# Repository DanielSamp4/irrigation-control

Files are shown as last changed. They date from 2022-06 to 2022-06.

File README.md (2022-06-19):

# Control plants irrigation using ESP32

A challenge made by Neurobots

# Overview

This project consist in creat a system that can irrigate plants based on day period and degree of humidity. This system have to be pownred by a battery of 3.7v 

### System

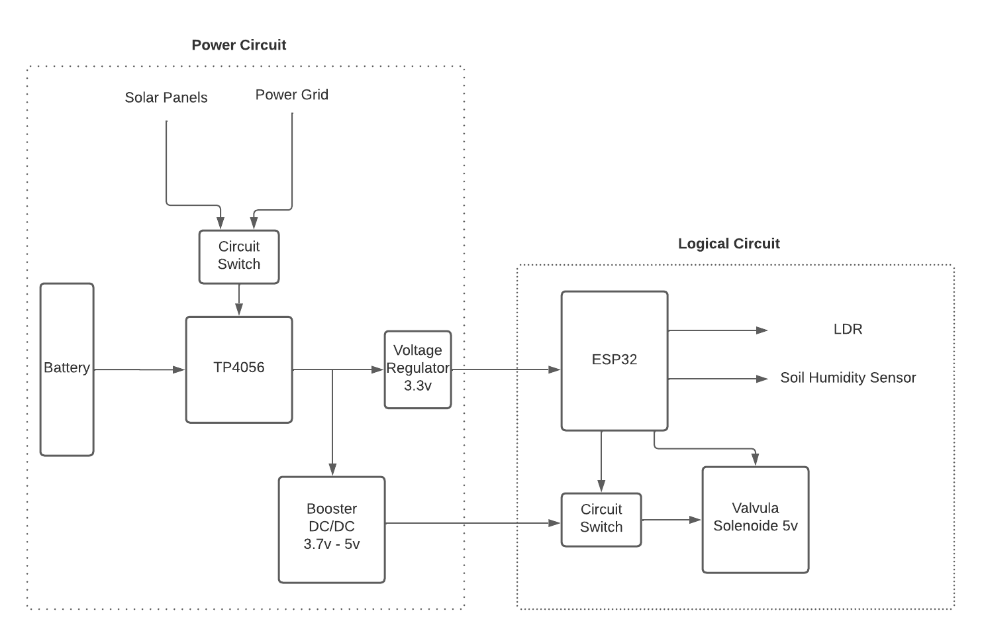
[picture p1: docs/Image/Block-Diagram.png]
Block Diagram
<div align="center">

 In summary, the system is made to charge the battery with solar pannels or power grid (giving priority to the power grid), and power a ESP32 that will be the brain operation, that will check if LDR and Soil Hmidity Sensor get in determinate condition, and will trigger the circuit switch to activate the solenoid, therefore irrigating a plant.

 The Soil Hmidity Sensor, Solenoid and LDR have conectors attached to the PCB (See Hardware Section) to connect them, and the user feel free to use them.
 
### Power Circuit
lithium batteries can be dangerous if not charged properly and that's why the TP4056 is useful as it stops over voltage and current charging by detecting specific voltage conditions. You should never use the TP4056 as a charger and as a load driver at the same time. For this we will use a PMOSFET that will function like a controlled switch that disconnects the battery when external power is applied. The TP4056 still charges the battery but without a load. Power to the load is supplied from the power source directly.

To know more about the right way to use TP4056 see https://www.best-microcontroller-projects.com/tp4056.html

### Logical Circuit

Both LDR and Sensor Humidity are analog devices, therefore can be atached to any ADC GPIO of ESP32, i choose GPIO 34 and 35 (See Firmware Section).

For Activate the solenoid, must be a output GPIO (anyone except 34, 35, 36, 39 because they are input only) and the circuit switch will be a NMOSFET with gate connect to GPIO, drain connect to GND from the solenoid and source connect to GND from the circuit, with this configuration when GPIO is high the NMOSFET will connect the GND from NMOSFET with the GND from de circuit and de valvula solenoid will open. I will connect to GPIO 25 and will use PWM signal to see if will genarate some kind of water flow control from solenoid.

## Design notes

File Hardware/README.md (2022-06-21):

# Hardware

### Schematic
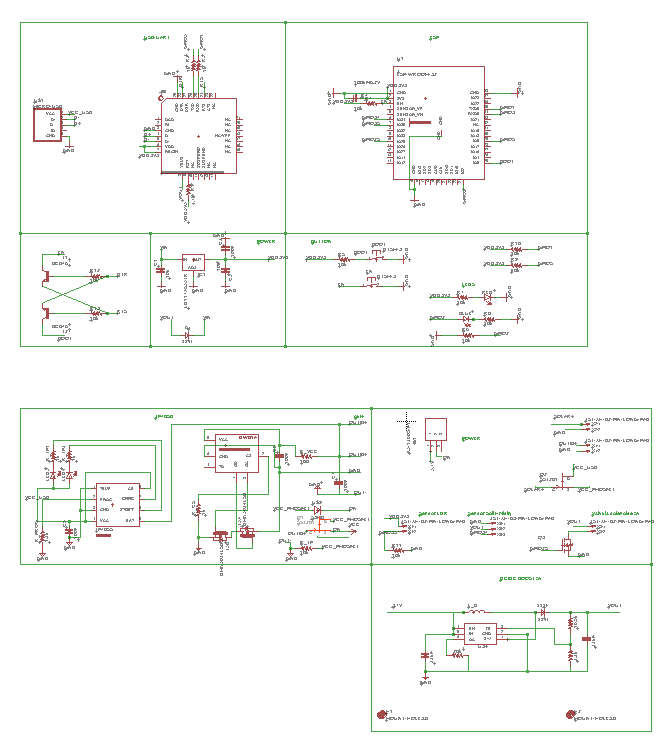
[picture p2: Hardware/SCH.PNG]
Schematic
<div align="center">

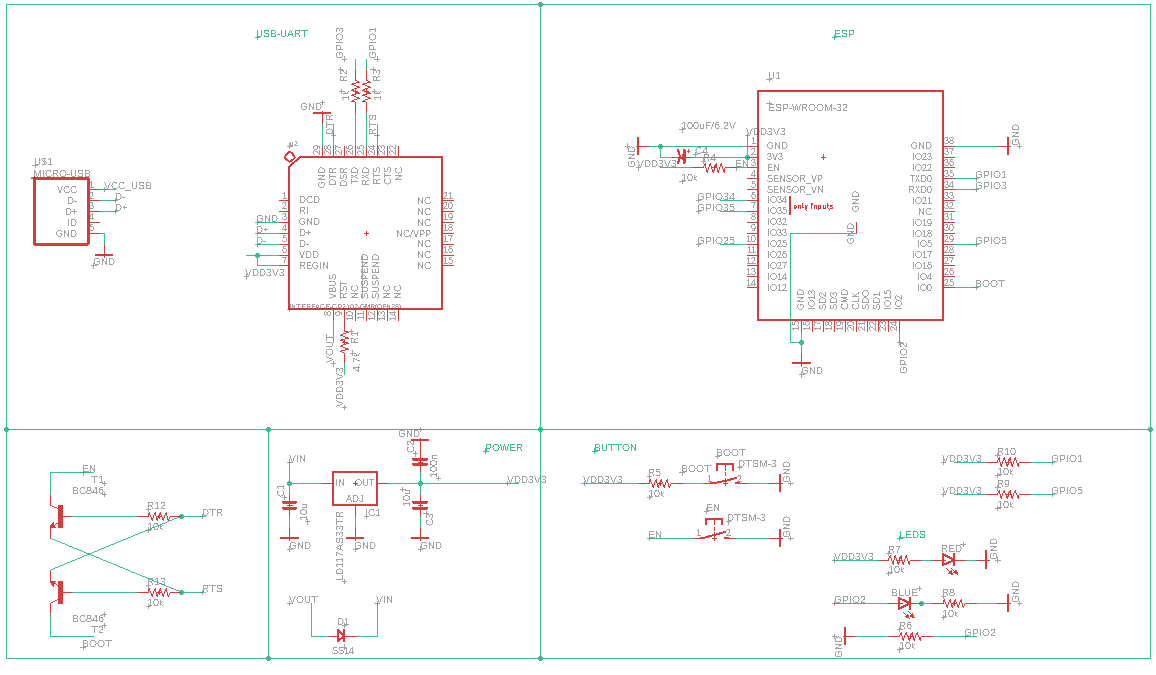
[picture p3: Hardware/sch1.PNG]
Schematic part 1
<div align="center">

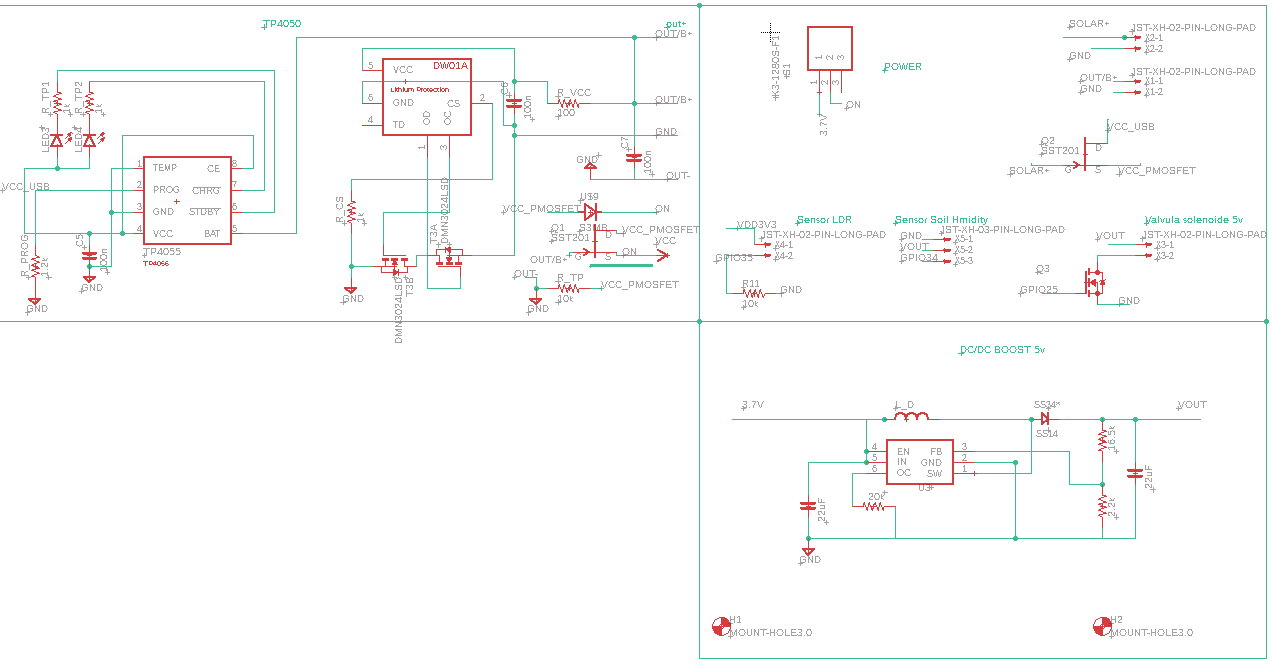
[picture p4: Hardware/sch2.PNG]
Schematic part 2
<div align="center">

### Board
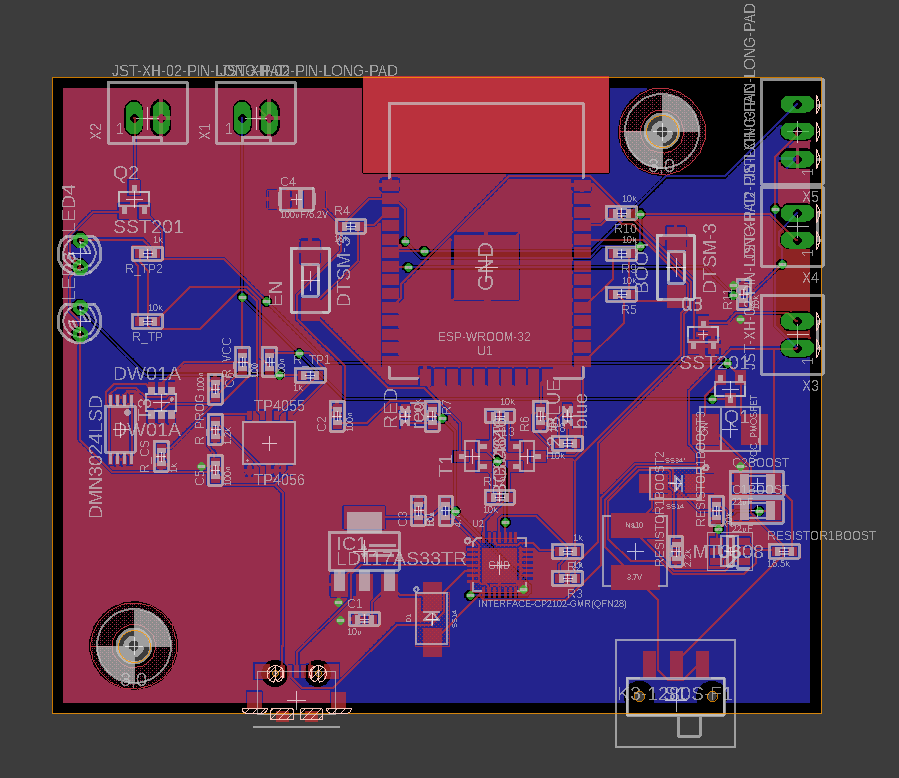
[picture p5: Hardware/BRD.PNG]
Board
<div align="center">

### Manufactoring
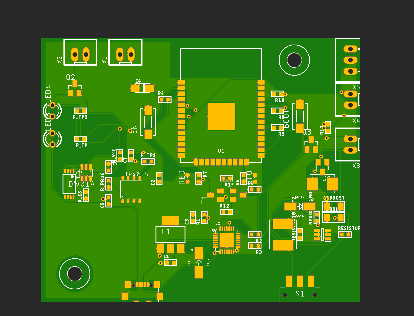
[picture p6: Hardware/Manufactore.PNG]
Manufactoring
<div align="center">

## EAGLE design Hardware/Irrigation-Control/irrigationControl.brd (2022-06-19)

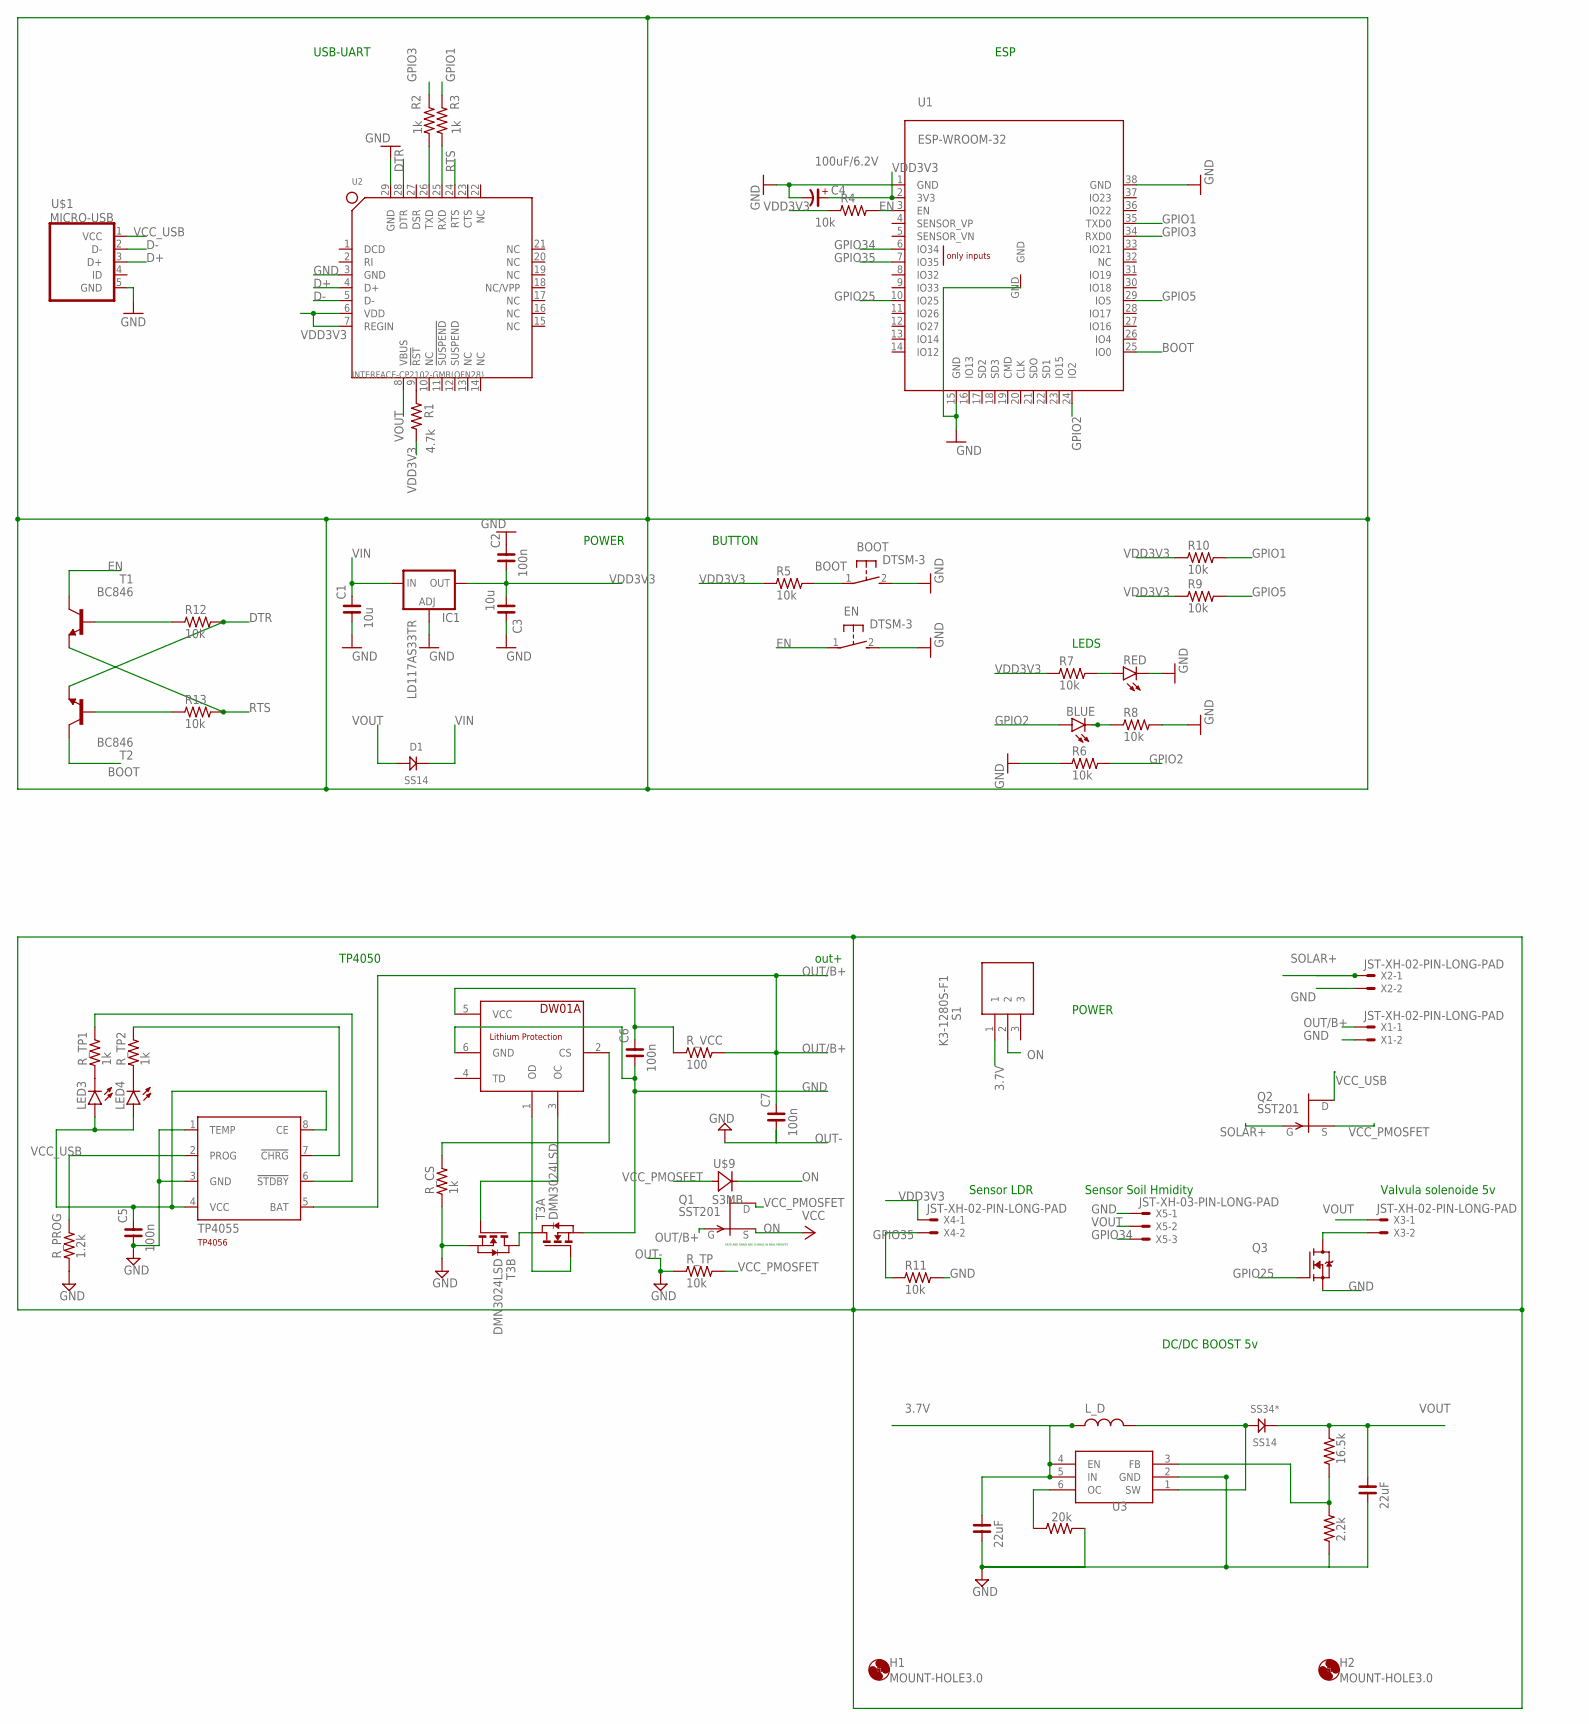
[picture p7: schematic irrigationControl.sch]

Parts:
BLUE: blue; CHIPLED_0603
BOOT: DTSM-3
C1, C3: 10u; C0603
C1BOOST, C2BOOST: 22uF; C1206
C2, C5, C6, C7: 100n; C0603
C4: 100uF/6.2V; C3216-18/T
D1: SS14; DO214
DW01A: DW01A; SOT23-6
EN: DTSM-3
H1, H2: MOUNT-HOLE3.0; 3,0
IC1: LD117AS33TR; SOT223
LED3, LED4: LED3MM
L_D: SLW6045S221MST
Q1, Q2: SST201; SOT23
Q3: TRANSISTOR_FET_BS170-SOT-23; SOT-23
R1: 4.7k; R0603
R2, R3: 1k; R0603
R4, R5, R6, R7, R8, R9, R10, R11, R12, R13: 10k; R0603
RED: red; CHIPLED_0603
RESISTOR1BOOST: 16.5k; R0603
RESISTOR1BOOST2: 2.2k; R0603
RESISTOR1BOOST3: 20k; R0603
R_CS: 1k; R0603
R_PROG: 1.2k; R0603
R_TP: 10k; R0603
R_TP1, R_TP2: 1k; R0603
R_VCC: 100; R0603
S1: K3-1280S-F1; K31280SF1
SS34*: SS14; DO214
T1, T2: BC846; SOT23
T3: DMN3024LSD; TSSOP-8
TP4055: TP4056; SOT23-8
U1: ESP-WROOM-32
U2: INTERFACE-CP2102-GMR(QFN28); QFN28G_0.5-5X5MM
U3: MT3608; SOT95P280X145-6N
U$1: MICRO-USB; MICRO-USB-2
U$9: S3MB
X1, X2, X3, X4: JST-XH-02-PIN-LONG-PAD; JST-XH-02-PACKAGE-LONG-PAD
X5: JST-XH-03-PIN-LONG-PAD; JST-XH-03-PACKAGE-LONG-PAD

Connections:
3.7V: C1BOOST.2, L_D.1, S1.1, U3.4 (EN), U3.5 (IN)
BOOT: BOOT.1, R5.2, T2.3 (C), U1.25 (IO0)
D+: U2.4 (D+), U$1.3 (D+)
D-: U2.5 (D-), U$1.2 (D-)
DTR: R12.2, T2.2 (E), U2.28 (DTR)
EN: EN.1, R4.2, T1.3 (C), U1.3 (EN)
GND: BOOT.2, C1.1, C1BOOST.1, C2.2, C2BOOST.1, C3.2, C4.-, C5.1, C6.1, DW01A.6 (GND), EN.2, IC1.1 (ADJ), Q3.2 (S), R6.1, R8.2, R11.2, RED.C, RESISTOR1BOOST2.1, RESISTOR1BOOST3.1, R_CS.1, R_PROG.1, T3.2 (S), T3.3 (S), T3.6 (S), T3.7 (S), TP4055.1 (TEMP), TP4055.3 (GND), U1.1 (GND), U1.15 (GND), U1.38 (GND), U1.GND, U2.3 (GND), U2.29 (GND), U3.2 (GND), U$1.5 (GND), X1.2, X2.2, X5.1
GPIO1: R3.1, R10.2, U1.35 (TXD0)
GPIO2: BLUE.A, R6.2, U1.24 (IO2)
GPIO3: R2.1, U1.34 (RXD0)
GPIO5: R9.2, U1.29 (IO5)
GPIO25: Q3.1 (G), U1.10 (IO25)
GPIO34: U1.6 (IO34), X5.3
GPIO35: R11.1, U1.7 (IO35), X4.2
unnamed: R1.1, U2.9 (!RST)
unnamed: R2.2, U2.26 (TXD)
unnamed: R3.2, U2.25 (RXD)
unnamed: R12.1, T1.1 (B)
unnamed: R13.1, T2.1 (B)
unnamed: BLUE.C, R8.1
unnamed: Q3.3 (D), X3.2
unnamed: L_D.2, SS34*.ANODE, U3.1 (SW)
unnamed: RESISTOR1BOOST.1, RESISTOR1BOOST2.2, U3.3 (FB)
unnamed: RESISTOR1BOOST3.2, U3.6 (OC)
unnamed: LED3.K (C), R_TP1.1
unnamed: LED4.K (C), R_TP2.1
unnamed: R7.2, RED.A
unnamed: R_TP2.2, TP4055.7 (!CHRG)
unnamed: R_TP1.2, TP4055.6 (!STDBY)
unnamed: R_PROG.2, TP4055.2 (PROG)
unnamed: T3.1 (D), T3.8 (D)
unnamed: DW01A.3 (OC), T3.5 (G)
unnamed: DW01A.2 (CS), R_CS.2
unnamed: DW01A.1 (OD), T3.4 (G)
unnamed: C6.2, DW01A.5 (VCC), R_VCC.1
ON: Q1.2 (S), S1.2, U$9.-
OUT-: C7.1, R_TP.1
OUT/B+: C7.2, Q1.3 (G), R_VCC.2, TP4055.5 (BAT), X1.1
RTS: R13.2, T1.2 (E), U2.24 (RTS)
SOLAR+: Q2.3 (G), X2.1
VCC_PMOSFET: Q1.1 (D), Q2.2 (S), R_TP.2, U$9.+
VCC_USB: C5.2, LED3.A, LED4.A, Q2.1 (D), TP4055.4 (VCC), TP4055.8 (CE), U$1.1 (VCC)
VDD3V3: C2.1, C3.1, C4.+, IC1.4 (OUT), R1.2, R4.1, R5.1, R7.1, R9.1, R10.1, U1.2 (3V3), U2.6 (VDD), U2.7 (REGIN), X4.1
VIN: C1.2, D1.CATHODE (KATHODE), IC1.3 (IN)
VOUT: C2BOOST.2, D1.ANODE, RESISTOR1BOOST.2, SS34*.CATHODE (KATHODE), U2.8 (VBUS), X3.1, X5.2

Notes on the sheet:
POWER
ESP
USB-UART
BUTTON
LEDS
GATE AND DRAIN ARE CHANGE IN REAL PMOSFET
TP4050
out+
DC/DC BOOST 5v
Sensor LDR
Sensor Soil Hmidity
Valvula solenoide 5v

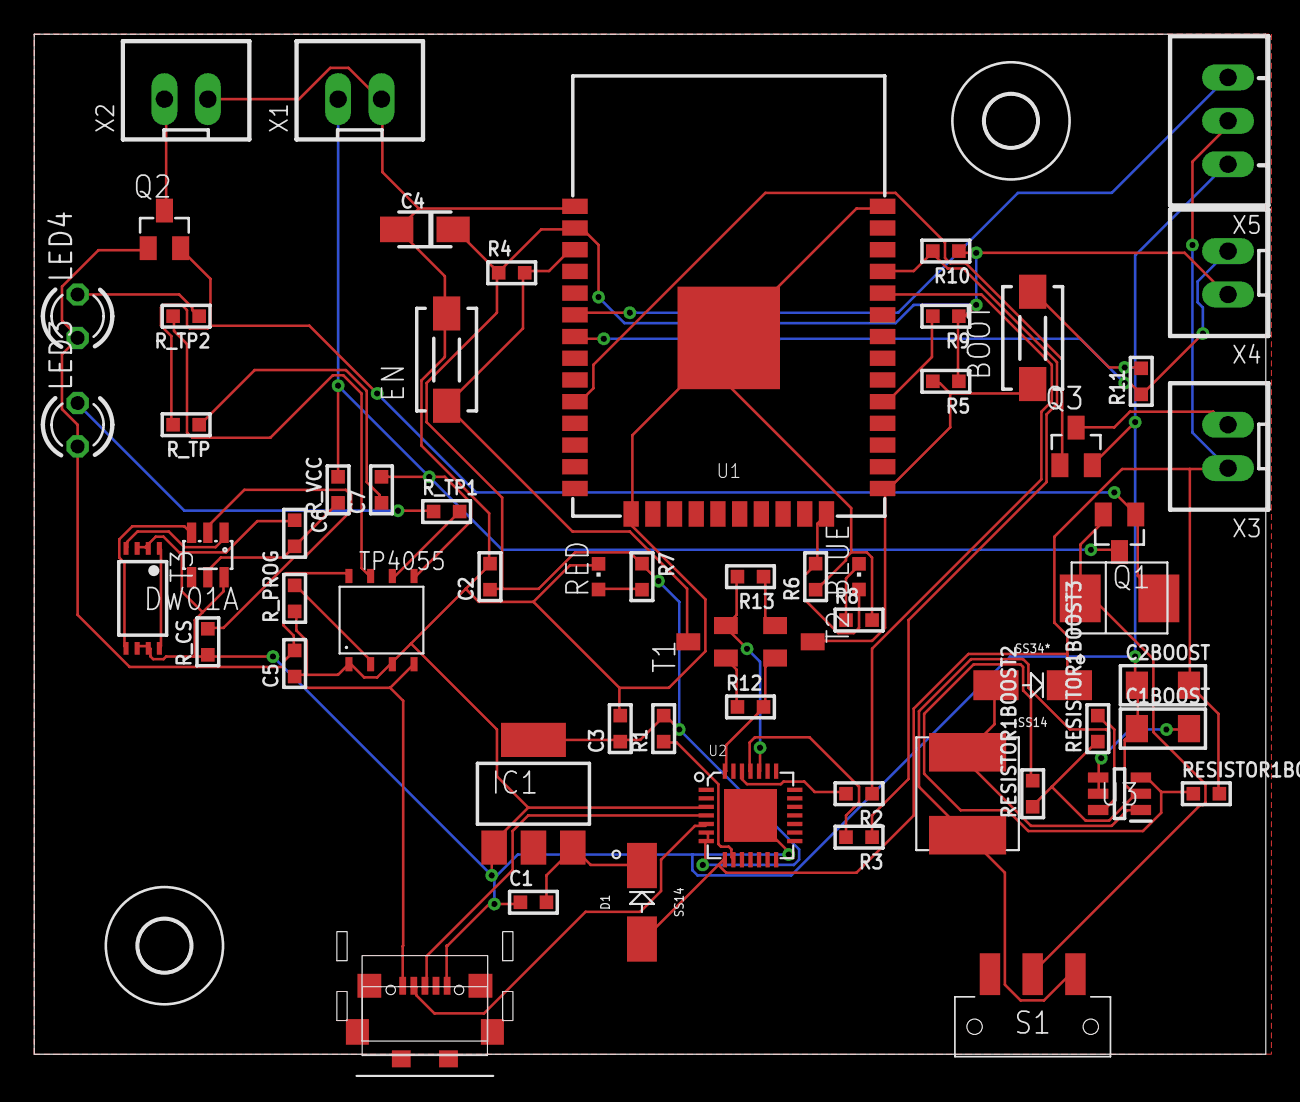
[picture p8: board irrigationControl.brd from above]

Board: 2 copper layers, 72.1 x 59.7 mm, 62 parts (0 on the bottom side), 45 nets.

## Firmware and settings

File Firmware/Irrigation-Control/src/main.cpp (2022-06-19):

/**
 *	Firmware to run the project Irrigation-control 
 *	@file irrigation-control
 *	@author	daniel.sampaio0144@gmail.com
 *	@version	1.0
 *	@date	2022-06-19
 */

#include <Arduino.h>

#define LDR 35
#define Soil_Humidity 34
#define Solenoid 25

#define Condition_LDR 100 // here you put your conditions of LDR
#define Condition_Soil_Humidity 100 // here you put your conditions of Soil_Humidity

void setup() {
  Serial.begin(115200);
  pinMode(Solenoid, OUTPUT);
}

//some feature implamentation will be use sleep mode on  ESP32 to save energy for battery
void loop() {
if (analogRead(LDR) < Condition_LDR && analogRead(Soil_Humidity) > Condition_Soil_Humidity)
  digitalWrite(Solenoid,HIGH);
else  
  digitalWrite(Solenoid,LOW);
}

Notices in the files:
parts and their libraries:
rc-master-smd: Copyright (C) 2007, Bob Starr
